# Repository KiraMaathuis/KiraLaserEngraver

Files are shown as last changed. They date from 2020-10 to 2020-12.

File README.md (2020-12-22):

# CoreXY Laser Engraver and Pen Plotter
This is my repository to document my laser engraver project. It has gone through multiple iterations and currently is inspired by the [H-bot](https://openbuilds.com/?id=274) design.

This is a new version which is a bit smaller in form, as my last design was still to big for my student studio. I also haven't used the laser yet as I do not have a safe enclosure, so I just use it as a pen plotter right now.

## Design goals and constraints
* The XY-plane covered by the laser must be minimum 200 by 200 mm (This design is theoretically 200mm by infinite)
* The motors moving the laser on the XY-plane must be stationary.
* The laser must be able to cut 3mm multiplex, preferably 5mm.
* The machine must be rigid enough to not need fixture onto anything.
* The machine must be quiet enough to be used within my student studio.

## To do
* Add clamps to allow for a glass/wooden bed
* Design an enclosure for the controllers and power supplies
* Design an enclosure for safety
* Design a fume extraction method

## Current design overview

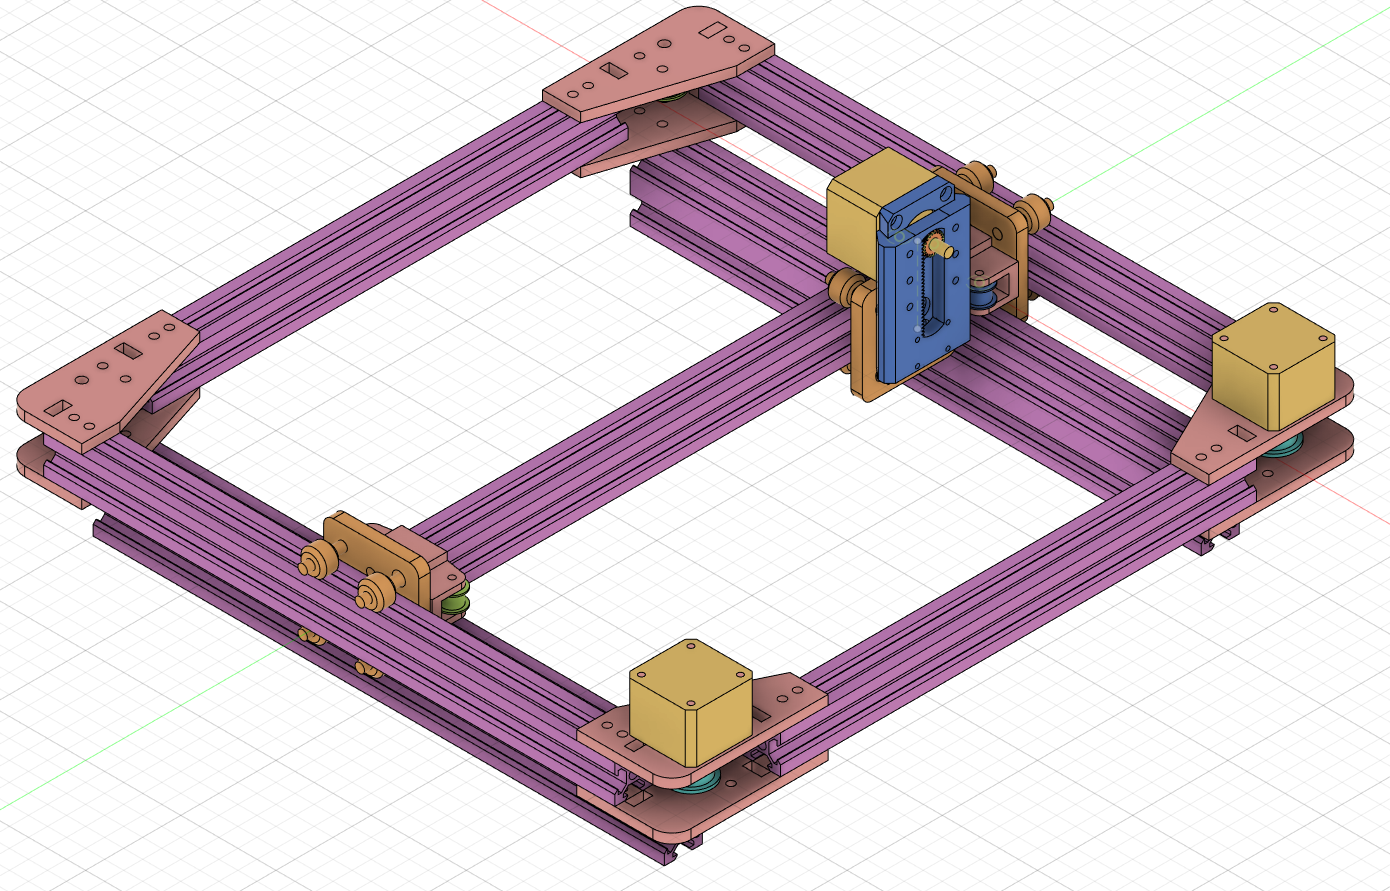
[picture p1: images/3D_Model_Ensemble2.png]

*All of the tan colored items and the blue pinion and rack in the picture above are 3D printed parts. Others are not.*

## Parts used
Not 3D printed:
* 2x 250mm 2020 Vslot extrusion
* 3x 300mm 2020 Vslot extrusion
* 2x 300mm 2040 Vslot extrusion
* 3x [Mini Vslot gantry](https://grabcad.com/library/mini-v-gantry-kit-1)
* 4x [F625ZZ flanged ball bearing](https://reprap.org/wiki/Ball_bearing)
* 4x [GT2Pulley](https://www.tinytronics.nl/shop/nl/3d-printen/onderdelen/gt2-16-pulley-tandloos-3mm-as-met-rollager)
* 2x [Belt (G2T) Pulley 30 teeth](https://grabcad.com/library/gt2-timing-pulley-30-tooth-1)
* 1x [G2T timing belt](https://reprap.org/wiki/GT2_Timing_Belt)
* 3x [Nema 14 motors](https://www.omc-stepperonline.com/nema-14-stepper-motor/nema-14-bipolar-1-8deg-14ncm-20oz-in-0-4a-12v-35x35x26mm-4-wires.html)
* 1x [3.5 Watt laser module (includes driver and power supply)](https://www.banggood.com/nl/LA03-3500-450nm-3_5W-Blue-Laser-Module-TTL-Modulation-Fan-Heat-Sink-for-EleksMaker-DIY-Engraver-p-1103261.html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)
* 1x [Arduino Uno](https://store.arduino.cc/arduino-uno-rev3)
* 1x [CNC shield v3](https://blog.protoneer.co.nz/arduino-cnc-shield/)
* 1x [40 Watt 12V power supply](http://www.meanwell.nl/products/Meanwell-RS-50-12---PSU-enclosed-12V-42A__RS-50-12.aspx)

3D printed:
* 2x motor plate for 2020 extrusion mount [model](./3D_prints/current/XaxisMotorMount.stl)
* 2x top plate for 2020 extrusion mount [model](./3D_prints/current/XaxisMotorTop.stl)
* 4x [model](./3D_prints/current/XaxisPulleyMount.stl)
* 8x [2020blocker](./3D_prints/current/2020Blocker.stl)
* 2x [YaxisMount](./3D_prints/current/YaxisMount.stl)
* 1x [PinionRackA](./3D_prints/current/PinionRackA.stl)
* 1x [PinionRackB](./3D_prints/current/PinionRackB.stl)

## Notes
* maybe letting the pinion and rack models be made out of metal will make the machine more rigid

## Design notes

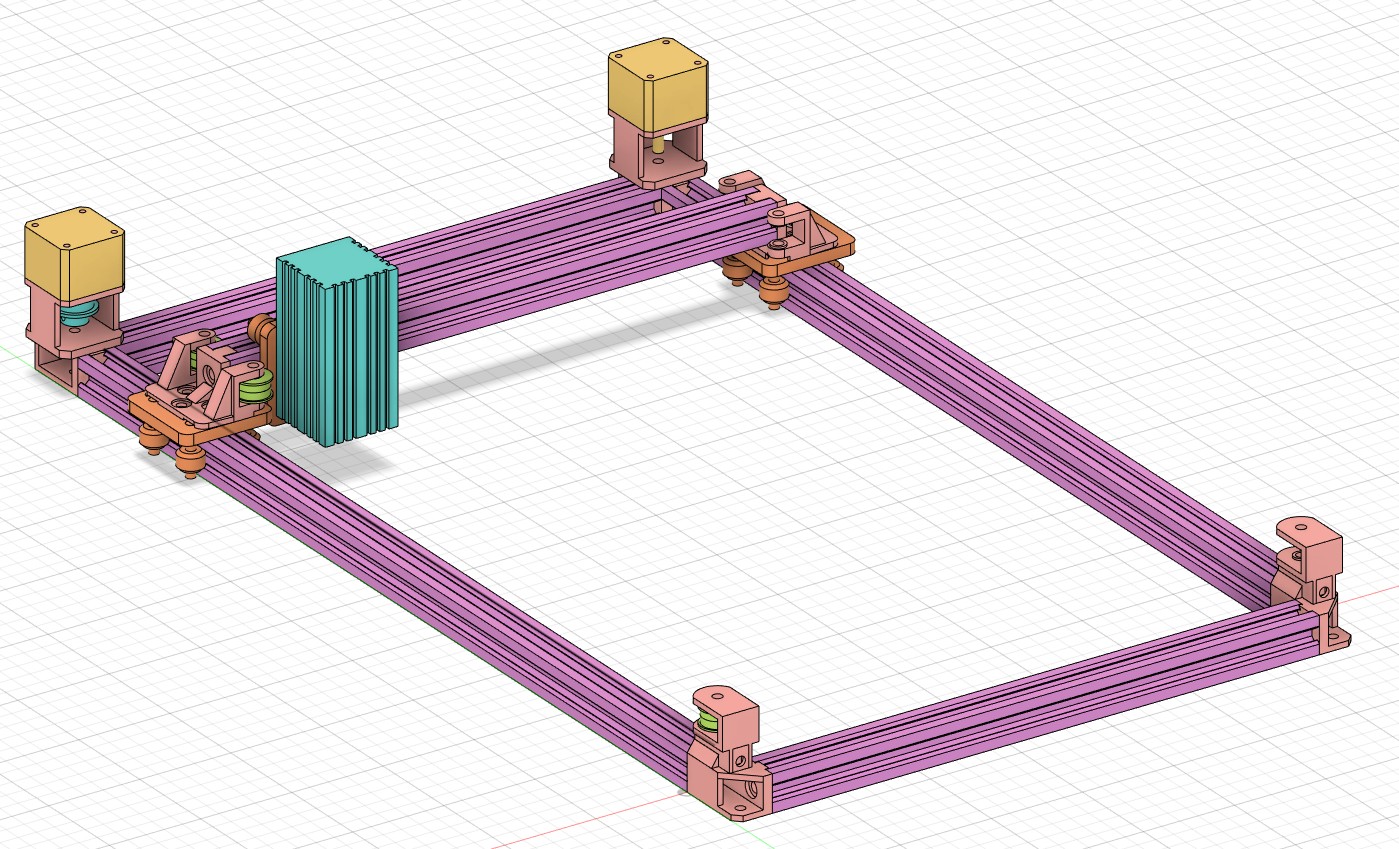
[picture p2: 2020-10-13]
images/3D_Model_Ensemble.png

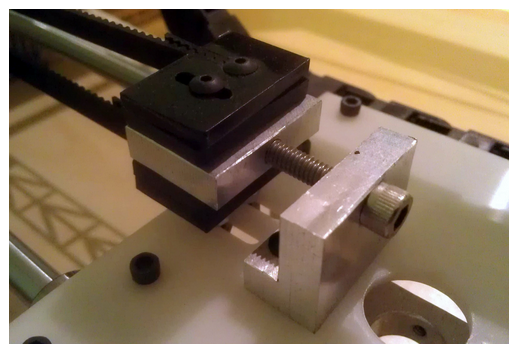
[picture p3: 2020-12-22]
images/belt_tensioner.png

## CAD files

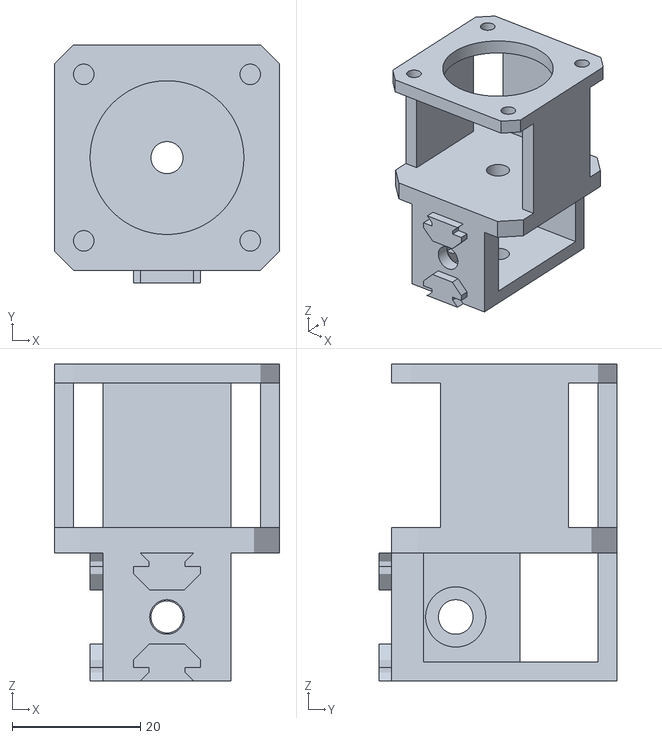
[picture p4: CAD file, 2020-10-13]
3D_prints/2020_Motor_R.stl
35.2 x 37.2 x 49.5

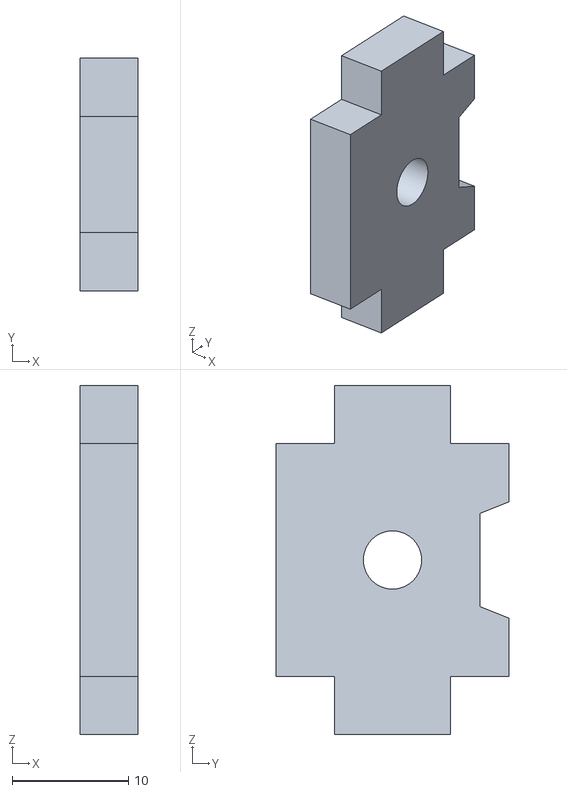
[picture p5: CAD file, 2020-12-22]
3D_prints/current/2020Blocker.stl
5.00 x 20.0 x 30.0

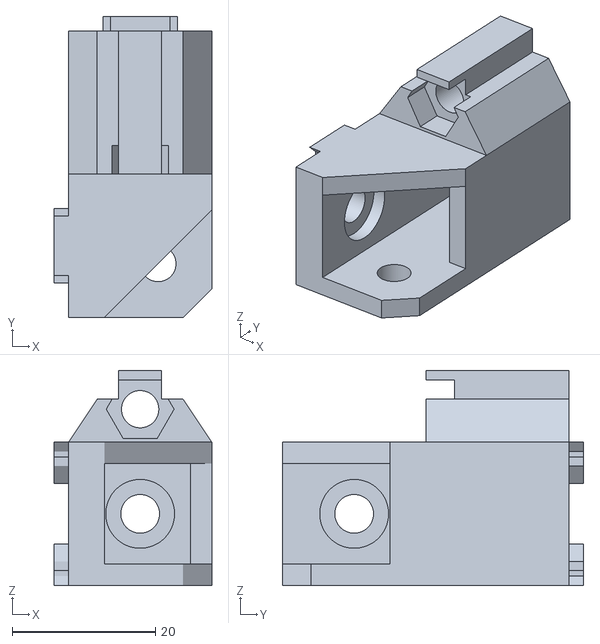
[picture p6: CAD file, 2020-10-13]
3D_prints/2020_Corner_R.stl
22.0 x 42.0 x 30.0

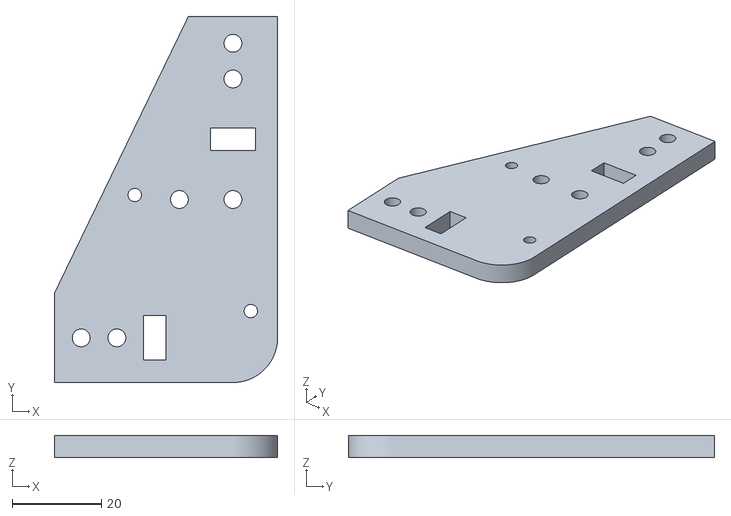
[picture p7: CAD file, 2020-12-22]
3D_prints/current/XaxisMotorTop.stl
50.0 x 82.0 x 5.00

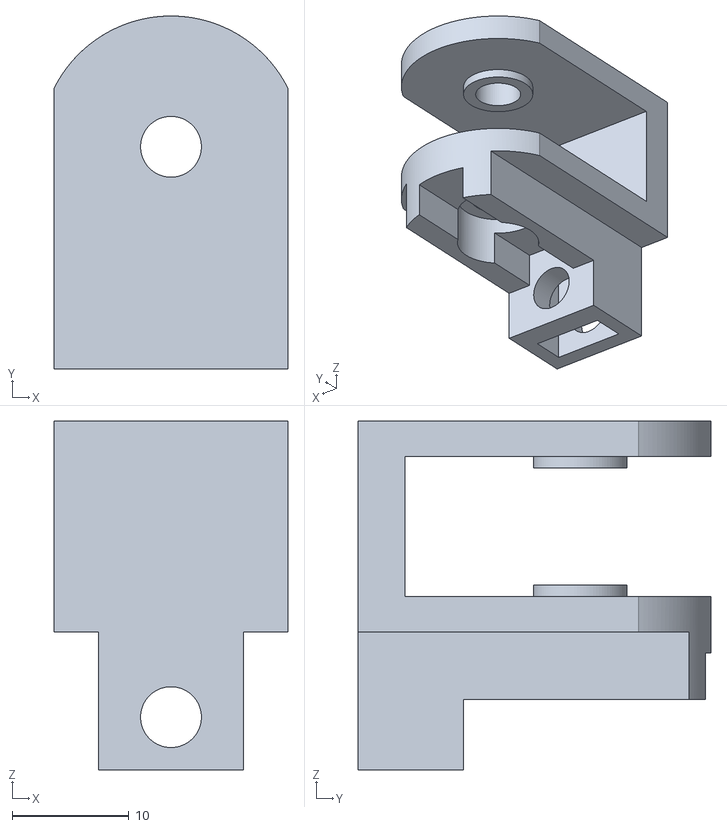
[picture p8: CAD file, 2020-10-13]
3D_prints/BeltTensioner.stl
20.0 x 30.2 x 29.8

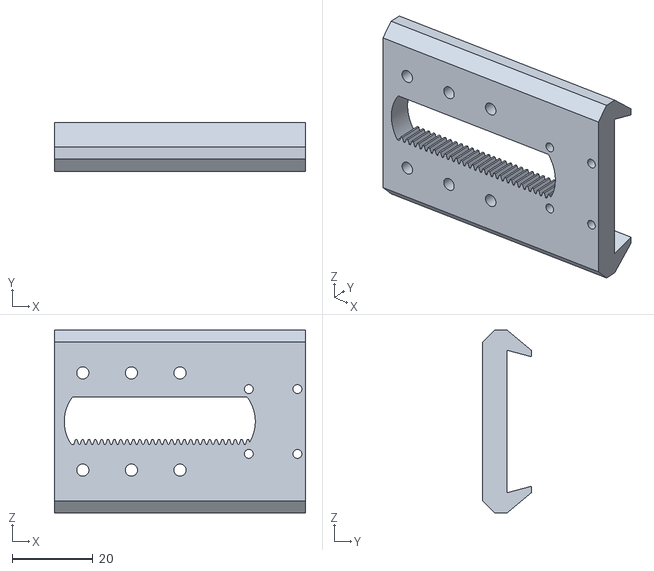
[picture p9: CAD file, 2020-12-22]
3D_prints/current/PinionRackB.stl
62.0 x 12.0 x 45.2

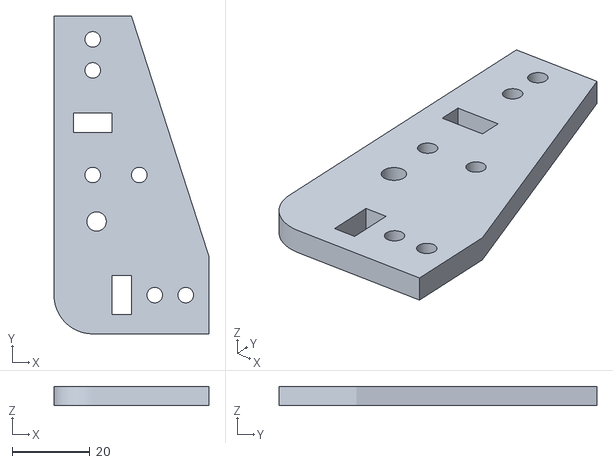
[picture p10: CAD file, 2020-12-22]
3D_prints/current/XaxisPulleyMount.stl
40.0 x 82.0 x 5.00

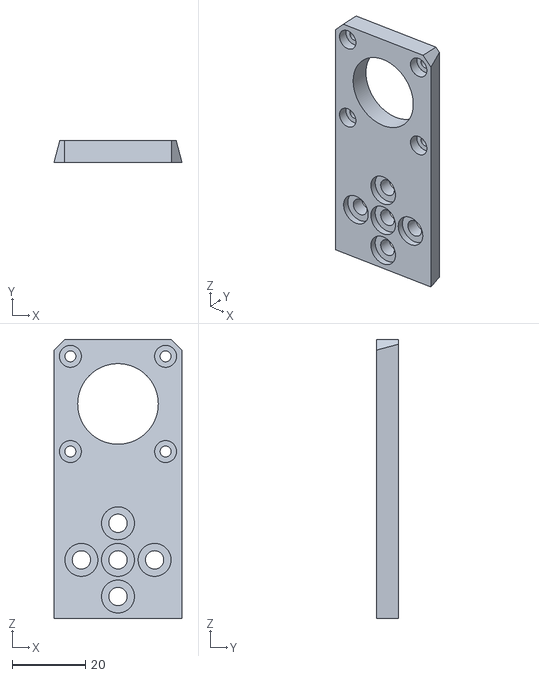
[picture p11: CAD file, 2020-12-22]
3D_prints/current/PinionRackA.stl
34.9 x 6.00 x 76.2

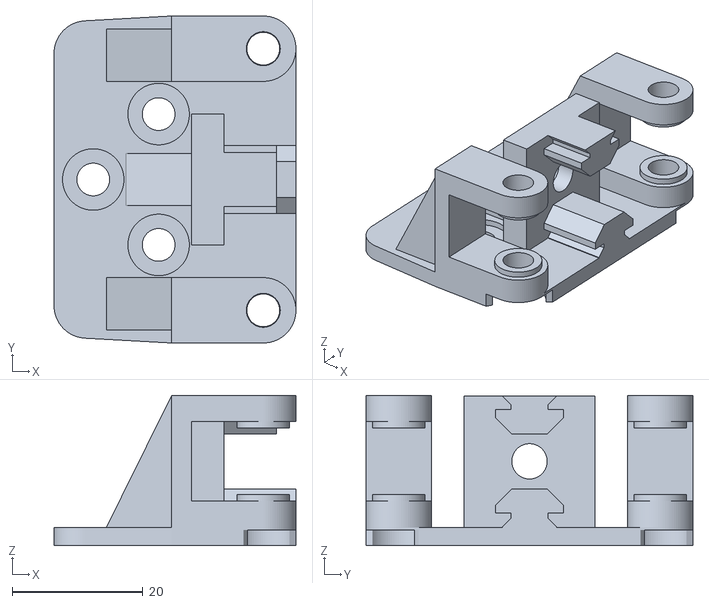
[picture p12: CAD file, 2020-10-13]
3D_prints/2020_Carriagemount.stl
37.0 x 50.0 x 23.0

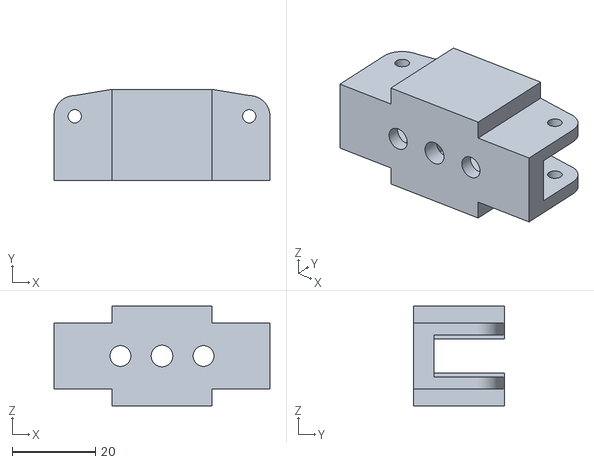
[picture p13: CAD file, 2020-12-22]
3D_prints/current/YaxisMount.stl
52.0 x 22.0 x 24.0

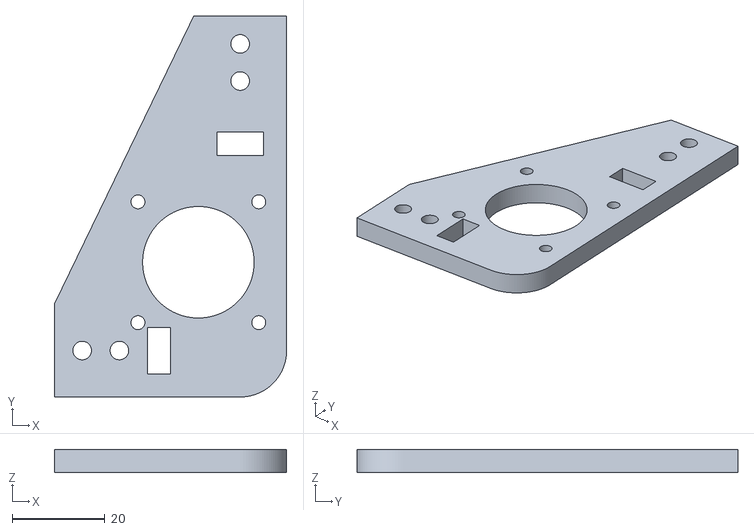
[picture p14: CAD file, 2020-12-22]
3D_prints/current/XaxisMotorMount.stl
50.0 x 82.0 x 5.00

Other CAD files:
3D_prints/2020_Motor_L.stl
3D_prints/2020_Corner_L.stl
3D_prints/old/2020_Corner_L.stl
3D_prints/old/2020_Motor_L.stl

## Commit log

2020-10-13 Design as of 13 oktober 2020.
    [2020_Carriagemount.stl, 2020_Corner_L.stl, 2020_Corner_R.stl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]
2020-10-13 Added Laser module
2020-12-22 New design
    [2020Blocker.stl, 2020_Carriagemount.stl, 2020_Corner_L.stl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]
